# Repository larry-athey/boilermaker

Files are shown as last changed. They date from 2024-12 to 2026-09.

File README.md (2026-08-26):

# Boilermaker

Advanced WiFi enabled ESP32 driven power controller and temperature regulator for brewing and distillation boilers. Multiple units can be combined in a master/slave configuration.

_**NEWSFLASH:** A smaller simplified version called [μBoilermaker (micro Boilermaker)](https://github.com/larry-athey/airhead/blob/main/Instructions/uBoilermaker.md) is now available for sale from my website. These are not WiFi-enabled and use the same guts as the [Airhead](https://github.com/larry-athey/airhead) running in a different operating mode._

You may contact me directly at https://panhandleponics.com<br>
Subscribe to the official YouTube channel at https://www.youtube.com/@PanhandlePonics

**Facebook Idiot:** _Why would you bother?_<br>
**Me:** It's only a "bother" for somebody who couldn't do it on their best day. I'd rather have nicer things.

_...No, I don't use AI to design and build my projects, I actually still know how to use my brain..._

---

<br>

---

After dealing with one cheap Chinese SCR power controller after another I decided to combine one person's email suggestion about building a WiFi enabled PID controller and mash it up with what I had just finished building for Air Still users. PID controllers have their place, but I think they're better suited for 3D printers, fermenters, brew pots, ovens, incubators, etc. The heating element spends more time off than on and that is horribly bad for distilling because there's almost nil upward thermal velocity happening in your boiler.

So I came up with my own controller to overcome all of the shortcomings that I kept running into with others. The Boilermaker has 4 different operating modes.

1. Constant Power (similar to an SCR controller, but leaps and bounds better than an SCR controller)
2. Temperature Cruise (controlled chaos, fast linear temperature rise with a limited risk of scorching)
3. Brewing/Fermentation (PID controller, slow and easy heating with an extreme level of accuracy)
4. Cruise Then Brew (Runs mode 2 until the target temperature is reached and then switches to mode 3)

_**NOTE:** Mode 2 is the same temperature control method used in my [Airhead](https://github.com/larry-athey/airhead) upgrade for Air Stills. The progressive temperature feature is also implemented here and can be used in modes 2 and 3. The only difference here is that the Boilermaker doesn't turn off at the end of the progression unless the countdown timer is enabled._

This controller was designed to run a [zero-crossing trigger solid state relay](https://www.amazon.com/dp/B08FR13GYR) utilizing my custom low speed PWM _(most effective method for heating elements)_. My custom low speed PWM works like an SCR controller slowed down to less than 1/1000 the speed and runs heating elements much more effectively. This controller can also be used with an existing PWM controlled SCR board or a voltage controlled SCR board with a [PWM to voltage convertor module](https://www.amazon.com/dp/B0BG2G5FMX) in the middle.

Heating elements have a slow reaction time, they take time to warm up. An SCR controller divides your AC power sine wave into anywhere from 1000 to 20000 slices and then determines which back-to-back slices are on and which ones are off. Granted, this "works" for heating elements, but it's wasteful and never lets the heating element run at its full potential unless it's at 100%. Anything less just results in a lot of energy wasted by warming up the SCRs instead of the heating element. Exactly what benefit are hot SCRs providing?

In the low speed (0.1 Hz to 1 Hz) PWM that I came up with for the [Airhead](https://github.com/larry-athey/airhead) controller and implemented here, even at 50% power using 0.5 Hz, the heating element runs for 1.25 seconds and rests for 1.25 seconds. Most heating elements run for the full duration of their reaction time. Whereas when using an SCR controller, all heating elements only run for 0.008 seconds 60 times per second. See why a low speed PWM running an SSR is better?

The greatest benefit of this PWM and SSR combination is that it doesn't contribute to premature heating element failure as with the high-speed on/off switching in SCR controllers. SCR phase-angle control generates harmonics _(distortions in the AC sine wave)_ which leads to uneven current distribution, physical vibration, and stress within a heating element. The Boilermaker is actually better for your boiler's longevity!

The Boillermaker uses either a DS18B20 temperature sensor or a thermocouple and a MAX-6675/MAX-31855 amplifier module. If your intention is to only use this controller with a distillation boiler or a meat smoker, then the DS18B20 is perfectly fine since it has an upper temperature limit of 125C/257F. If you need a higher temperature range, you will need to use the [Web API call](https://github.com/larry-athey/boilermaker/blob/main/Instructions/WebAPI.md) with your web browser to select the MAX-6675/MAX-31855 amplifier combo instead.

The Boilermaker also features a complete [Web API](https://github.com/larry-athey/boilermaker/blob/main/Instructions/WebAPI.md) for configuration and control, this is how one master unit controls up to 4 slaves. Each of those slaves can also have up to 4 slaves _(look at it like an Amway pyramid scheme)_. This means that these controllers can be added to all kinds of systems out there that allow the use of external commands or API integration of third party devices and services.

The [RPi Smart Still](https://github.com/larry-athey/rpi-smart-still) system fully supports the Boilermaker in all three temperature managed modes. It can also run the Boilermaker the same way as an SCR controller or gas valve, but without the need for a stepper motor.

_**NOTE:** The Boilermaker is also handy for turning any cheap electric smoker into one that's a whole lot more reliable and accurate, see the [Usage Tips](https://github.com/larry-athey/boilermaker/blob/main/Instructions/Usage-Tips.md) for more information._

<br>
<br>


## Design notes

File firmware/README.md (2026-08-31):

# Firmware Updating

As of the Boilermaker v1.0.3 source code, end users can now update their firmware over-the-air using a web browser. The initial plan was to provide a USB firmware update utility, but the one that Espressif provides doesn't work like the Arduino IDE does and requires the user to perform circus tricks and learn to use a cryptic program that no non-techie will ever bother with.

To put the Boilermaker into firmware update mode, open the following URL with your web browser.

**http://boilermaker-ip/update-firmware** (where "boilermaker-ip" is the IP address of your Boilermaker)

The Boilermaker will start up a WiFi access point with the SSID **"Boilermaker-Updater"** and the password to connect is **"12345678"**.

Now open this URL: **http://192.168.4.1**

<br>

If you are unable to connect, check to make sure that your device pulled an IP address from the Boilermaker. If it does not pull one, you will need to manually configure a static IP address on your device. Here are settings that will work for you if you encounter this problem.

Address: 192.168.4.100<br>
Subnet Mask: 255.255.255.0<br>
Gateway: 192.168.4.1<br>
DNS: 192.168.4.1<br>

Click on the button to browse to your **boilermaker-firmware.bin** file and click the blue button to start the upload.

Once the upload progress bar has completed, the Boilermaker will reboot and will be running the new firmware.

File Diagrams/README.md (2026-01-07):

<br>

The instructions on this page are for my original prototype, shown in the above. It ain't pretty, but I still have my first one running my electric smoker to this day. The units that I sell on my website are based on the [Firefly PCB](https://github.com/larry-athey/boilermaker/tree/main/Diagrams/Firefly-PCB). The prototype model only requires the [Boilermaker-PSU-and-Interface](https://github.com/larry-athey/boilermaker/blob/main/Diagrams/Schematic_Boilermaker-PSU-and-Interface.pdf) to be wired up on a prototype PCB and connected to an ESP32 with breadboard jumper wires.

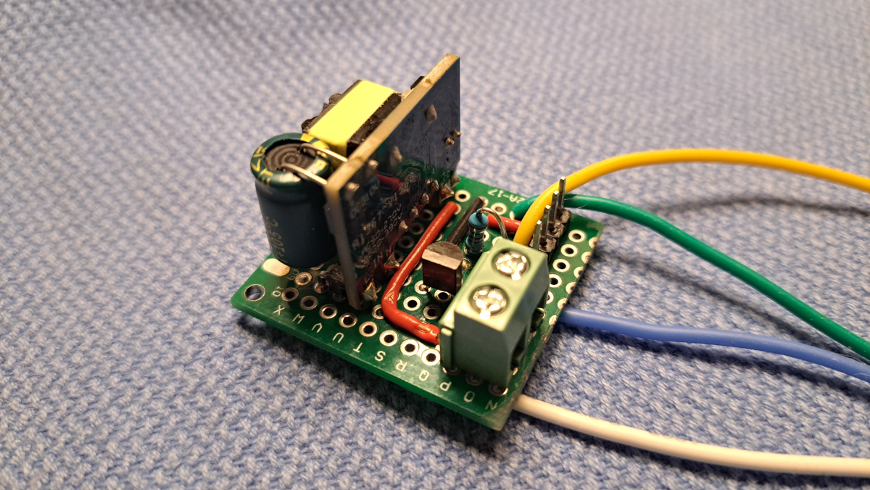
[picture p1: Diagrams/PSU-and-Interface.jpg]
<br>

As you can see, there's a whole lot of nothing to it. 4 wires come from it for the SSR + _(yellow)_, SSR - _(green)_, and two for the AC power input to the power supply _(blue and white)_. The cooling fan connects to the screw terminals _(+ on the left, - on the right)_. The 4-pin header is for the ESP32 for _(left to right)_ the fan trigger, SSR trigger, +5 volts, and ground. This only takes about an hour to assemble.

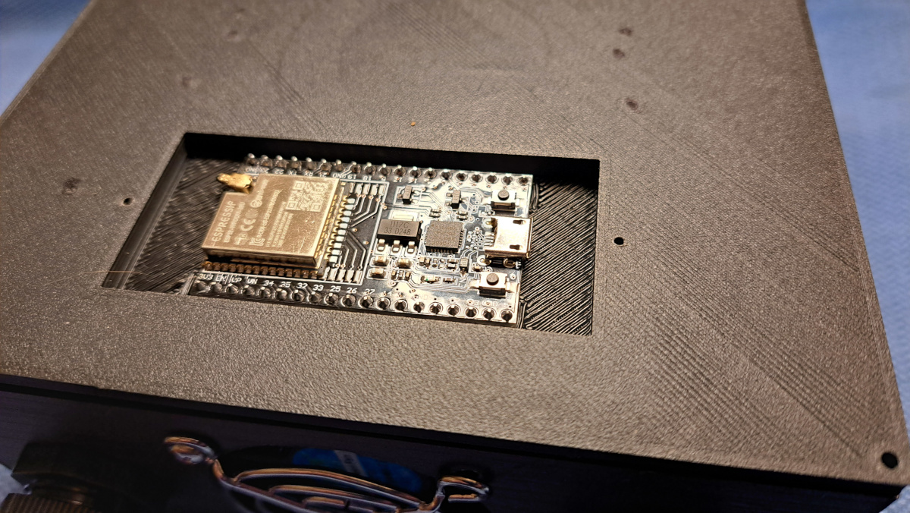
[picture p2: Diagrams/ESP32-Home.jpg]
<br>

As you can see in the **ESP32-Home.jpg** photo in the above, the ESP32 simply rests in the recessed cavity in the case cover. Another cover goes over this _(the **BM-ESP32-Cover.stl** model)_ to keep the ESP32 in place. This cavity is also big enough to hold the LilyGo ABS shell for their standard non-touch T-Display-S3 module. I've used a 38 pin WROOM-DA in this photo with an external antenna.

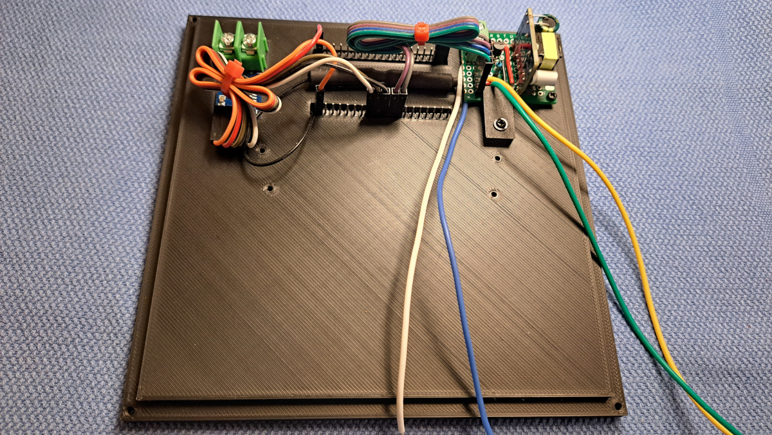
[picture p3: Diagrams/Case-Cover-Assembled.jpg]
<br>

In the **Case-Cover-Assembled.jpg** photo shown above, you can see the placement of the PSU and interface board, the MAX-6675 thermocouple amplifier, and the ribbon cables used to connect everything to the ESP32 pins. The external antenna is located between the rows of the ESP32 pins. If you bundle up the ribbon cables with zip ties, this will keep everything out of the way of the heatsink.

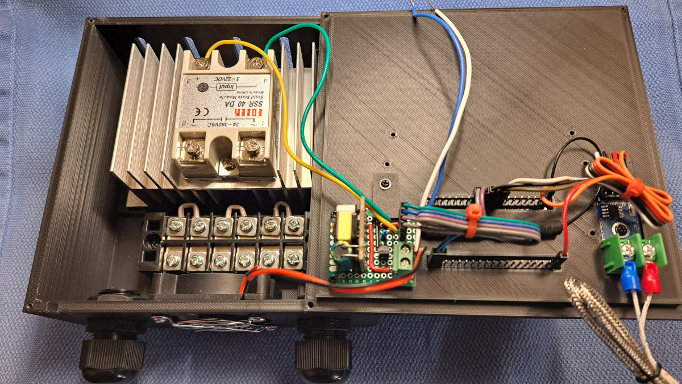
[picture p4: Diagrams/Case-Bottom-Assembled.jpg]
<br>

In the **Case-Bottom-Assembled.jpg** photo shown above, you can see the SSR and heatink as well as a screw terminal bus bar installed in the case bottom. The trigger wires to the SSR are connected and you would connect your AC power input/output lines at this point. Connect the ESP32 PSU input lines to the AC input side of the SSR and the bus bar. Honestly, it's totally up to you if you want to switch the AC hot or neutral line with the SSR, it honestly makes no difference. Connect the fan & thermocouple and you're done.

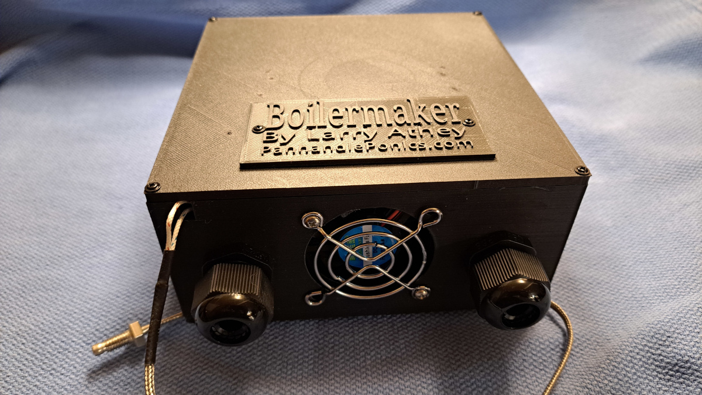
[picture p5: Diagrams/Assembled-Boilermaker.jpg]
<br>

And, as you can see in the **Assembled-Boilermaker.jpg** photo above, you have an assembled Boilermaker that's ready to go. Your choice of SSR will vary, depending on the load that you intend to run. Refer to the last section in the [Usage Tips](https://github.com/larry-athey/boilermaker/blob/main/Instructions/Usage-Tips.md) document for more information. While the amperage rating is important, the size of the heatink and having a cooling fan are equally important. You can very easily blow an SSR-100DA with a mere 1500 watt load if you don't keep it cool enough.

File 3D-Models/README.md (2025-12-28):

<br>

This case should print just fine on any 3D printer since it's not unnecessarily large. However this will not be a quick print due to the thickness of the walls, which is necessary since PLA printed items will warp if exposed to escessive heat. I'm not even joking for a minute, on a Creality Ender 5 Pro running at standard resolution and using 30% infill, the top of the case takes 8.5 hours and the bottom takes 21 hours with no supports. Making the walls thinner and reducing the infill doesn't have that much effect on the time.

_**NOTE:** You are free to use any resolution and infill rate of your choosing. I just use 30% infill by default for everything in order to make top surfaces smoother. The difference in print time between 15% and 30% isn't enough to make me lower my standards._

Using my settings with no supports for the bottom or ESP32 cover and the required supports for the ESP32 opening in the lid, below are the weights of each item so you will know how much filament that you need to have left on your roll.

Bottom - 185 grams<br>
Lid - 95 grams<br>
ESP32 Cover - 10 grams<br>

I intend to sell Boilermakers as assembled and tested units _(and pre-configured for the customer's WiF network)_, and I really can't afford to send out units where the case will warp due to excessive internal heat. $30 for a weather-proof ABS outdoor utility enclosure also doesn't make sense to me for something like this. Especially since a 1 KG roll of PLA filament is only $23 and I could print 5 cases.

This case was designed to accommodate an [SSR-40DA](https://www.amazon.com/Inkbird-Solid-Thermostat-Temperature-Controller/dp/B00HV974KC/) mounted to a [large SSR heat sink](https://www.amazon.com/uxcell-Aluminum-Dissipation-Single-10A-100A/dp/B07C8R7MS2/), and supports both a standard or wide format [38 Pin ESP32](https://www.amazon.com/gp/product/B09J95SMG7/). The ESP32 mounts in the lid and requires an additional cover _(**BM-ESP32-Cover.stl**)_ to be 3D printed to keep it in place.

The top of the case has a recessed footprint to mount a MAX-6675 thermocouple amplifier and screw holes to mount an Airhead PSU and Interface PCB. You will want to raise it with 1/4" spacers to allow room for jumper wire connections to the ESP32. It also provides screw holes for mounting various sizes of [prototye boards](https://www.amazon.com/ELEGOO-Prototype-Soldering-Compatible-Arduino/dp/B072Z7Y19F/) if you intend to build the PSU and interface according to the schematic in the **/Diagrams/** directory here. Use the **BM-PCB-Clamp.stl** to clamp down the side opposite of the screw holes.

This case also provides a footprint to mount a 6-column 90mm bus bar in the bottom for all AC power connections, and includes holes for 1/2" strain reliefs in case you decide to sacrifice a 12 gauge extension cord. Holes in the bottom of the case to the left and right of the bus bar are also provided in the event that you want to wall mount the unit.

There is also a 50mm fan mounting footprint between the AC power cable holes. You should install your fan so that it pulls cool air through the heat sink and evacuates the heat from the case. With most fans, this would mean the label side faces outward. I'd also suggest using a fan that comes with a guard/grill. This fan only runs when the Boilermaker is active so as not to fill it up with dust like a computer's cooling fan does.

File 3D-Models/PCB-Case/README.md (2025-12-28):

# 3D Model Notes

The models in this directory are for use with the PCB designed by [FireflySE](https://github.com/FireflySE) of Sweden. If you intend to sell assembled and tested Boilermakers, you will want to use the PCB and this case to make things easier on yourself. This case is 20mm longer than the one for prototype build and uses a different cover. This case is also 10mm taller in order to better accommodate 100 amp solid state relays.

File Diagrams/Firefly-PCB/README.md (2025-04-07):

# About this PCB

This is designed by [FireflySE](https://github.com/FireflySE) of Sweden, the same guy who designed the RPi Hat for the [RPi Smart Still](https://github.com/larry-athey/rpi-smart-still) controller system.

This board supports both, type-k thermocouple or DS18B20 temperature sensors. There is a [new version](https://github.com/larry-athey/boilermaker/tree/main/3D-Models/PCB-Case) of the Boilermaker case for use with this PCB. The origiinal case doesn't provide enough room to fit the PCB between the fan and SSR heatsink.

_**NOTE:** You will need to make one minor modification to my source code to work correctly with this PCB. My original code has the FAN_OUT constant pointing to GPIO 16, this PCB has it on GPIO 2. I have no idea what the reason was for the switch._

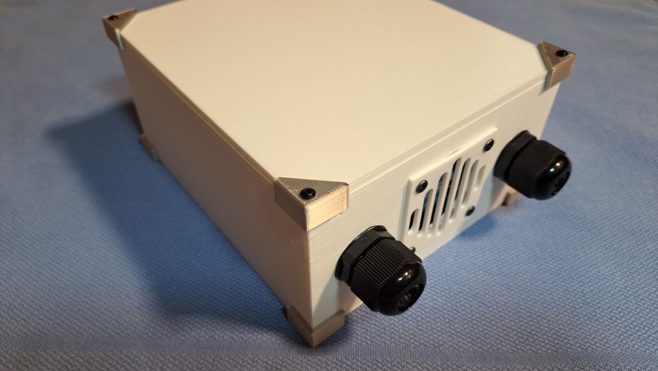
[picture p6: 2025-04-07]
3D-Models/PCB-Case/Boilermaker-1.jpg

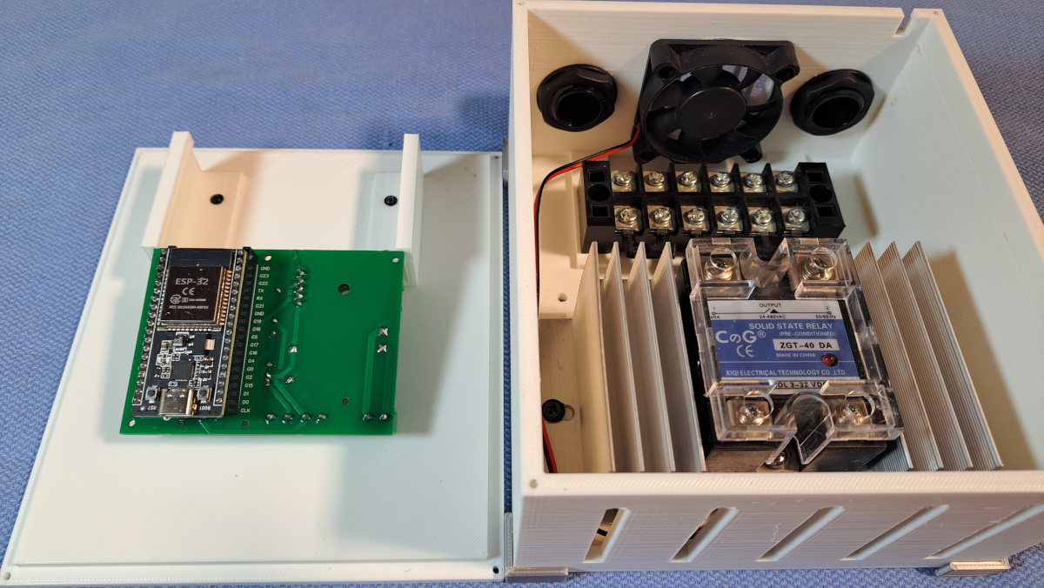
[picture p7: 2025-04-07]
3D-Models/PCB-Case/Boilermaker-3.jpg

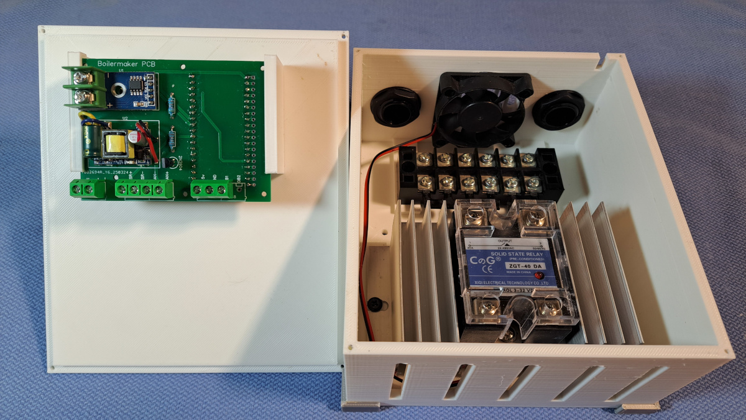
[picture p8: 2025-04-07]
3D-Models/PCB-Case/Boilermaker-2.jpg

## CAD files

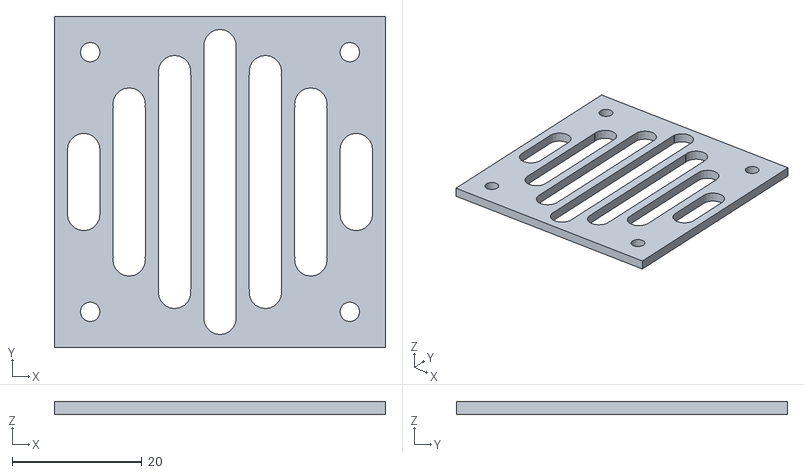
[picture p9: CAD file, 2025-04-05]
3D-Models/BM-Fan-Cover.stl
51.0 x 51.0 x 2.00

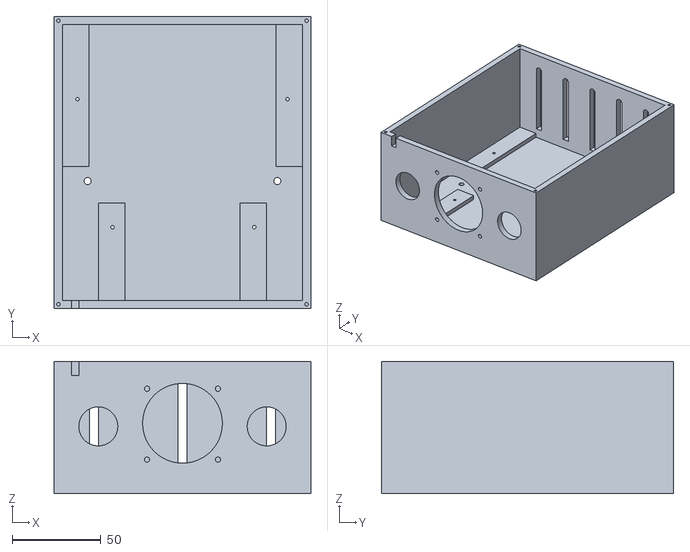
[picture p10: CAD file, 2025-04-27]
3D-Models/PCB-Case/BM-Case-Bottom.stl
145.0 x 165.0 x 74.8

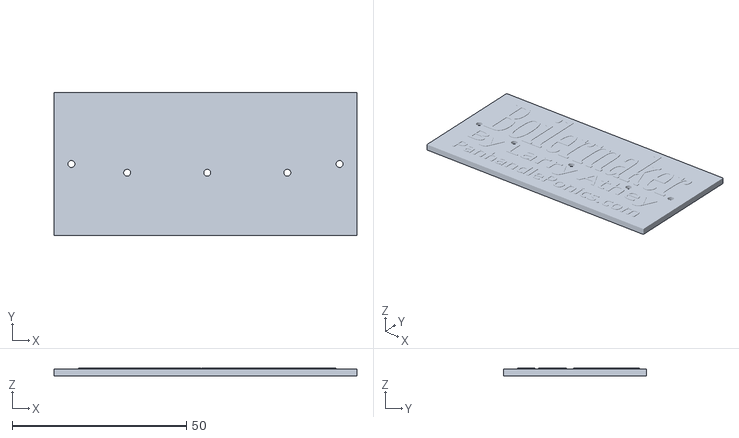
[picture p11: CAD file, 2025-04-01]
3D-Models/BM-ESP32-Cover.stl
87.0 x 41.0 x 2.25

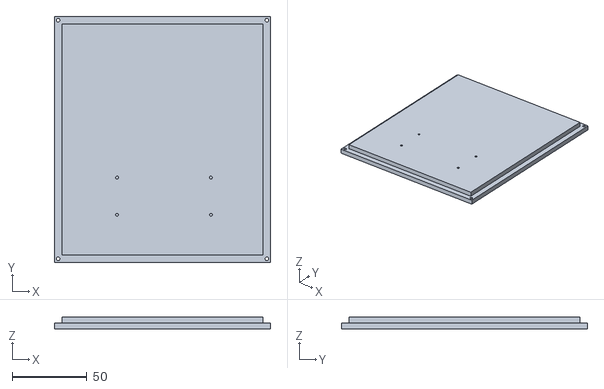
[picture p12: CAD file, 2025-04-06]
3D-Models/PCB-Case/BM-Case-Top.stl
145.0 x 165.0 x 8.00

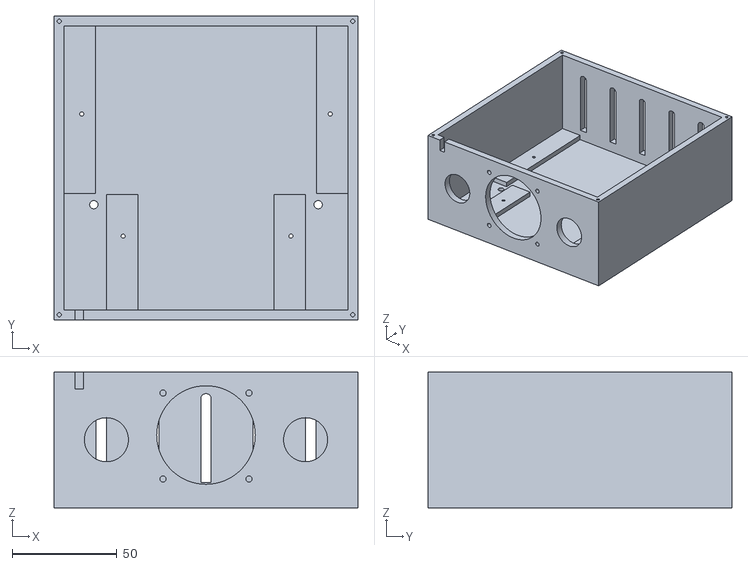
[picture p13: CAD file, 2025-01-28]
3D-Models/BM-Case-Bottom.stl
145.0 x 145.0 x 64.8

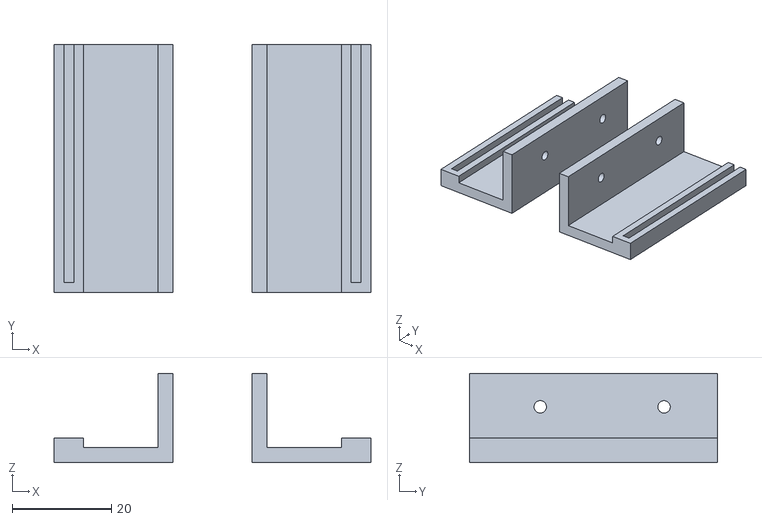
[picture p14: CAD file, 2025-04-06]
3D-Models/PCB-Case/BM-PCB-Mount.stl
64.0 x 50.0 x 18.0

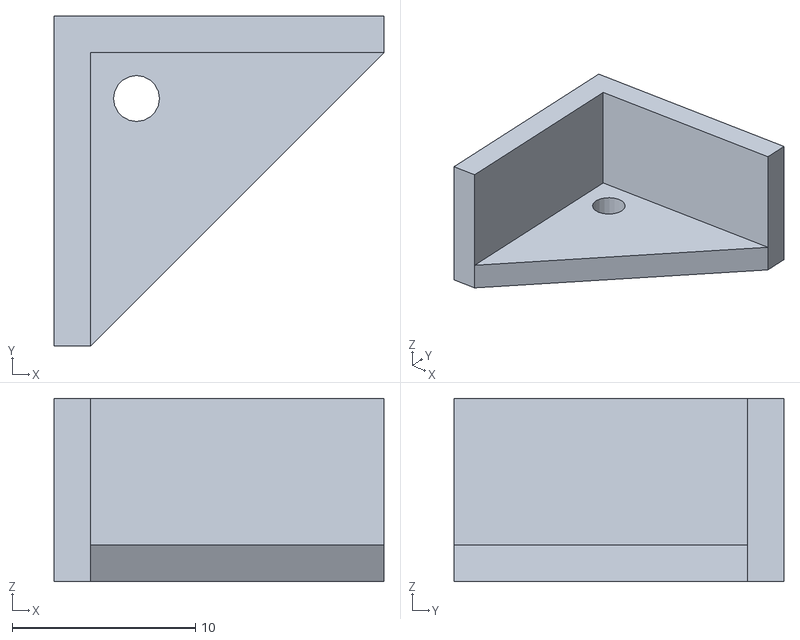
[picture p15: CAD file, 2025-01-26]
3D-Models/BM-Corner-Cap.stl
18.0 x 18.0 x 10.0

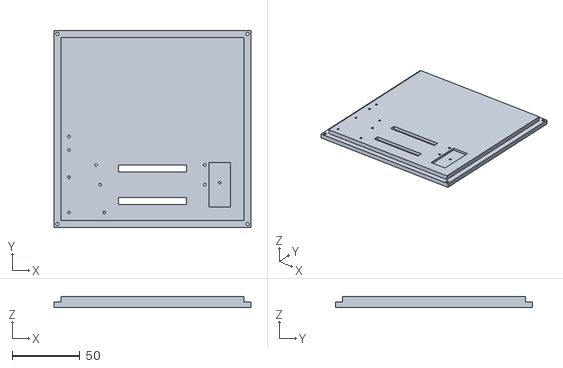
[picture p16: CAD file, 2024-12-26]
3D-Models/BM-Case-Top.stl
145.0 x 145.0 x 8.00

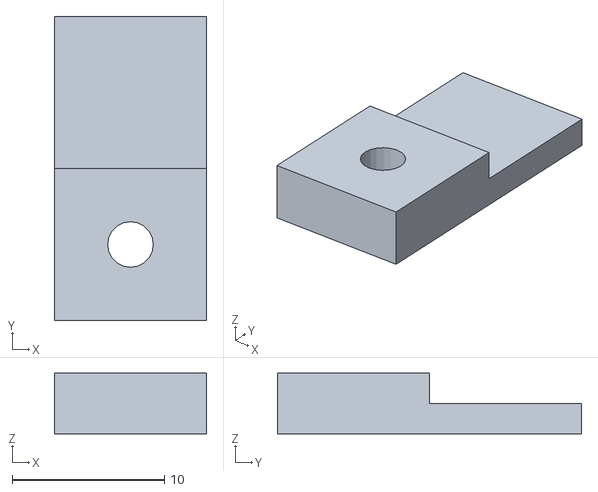
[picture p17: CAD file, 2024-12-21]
3D-Models/BM-PCB-Clamp.stl
10.0 x 20.0 x 4.00

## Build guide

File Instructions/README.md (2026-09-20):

# Instructions

<br>

_**IMPORTANT:** Please keep in mind that where you put your temperature sensor matters! No matter what you are using your Boilermaker for, you absolutely DO NOT want to be reading the temperature of your heating element! You need to be monitoring what you are boiling or the air around what you are smoking/roasting._

_**SECONDLY:** If your system appears to stop reading temperature changes when your temperature sensor comes in contact with your boiler, this means that your hot and neutral lines to the Boilermaker's internal power supply or the AC outlet itself are revesed. A quick (however unsafe) solution is to lift the ground connection, but you really should correct the polarity of the hot and neutral wires._

Unlike other WiFi enabled ESP32 powered devices, the Boilermaker does not default as a WiFi access point in order to configure it. I'm already using nearly 75% of the available code space, I don't want to waste the remaining 25% on a one-time-use feature. I'm reserving that 25% for future features and enhancements, so the WiFi configuration and a few other things are configured over a USB cable and a plain old terminal program. Windows doesn't include one by default anymore, but [PuTTY](https://www.putty.org/) is still free and open source.

[Here's how to use PuTTY under Windows to connect to the Boilermaker.](https://x.com/i/grok/share/i61lGPHt1tv3cxOr8ogD5S6SR)

Mac OS users should install the free [CoolTerm](https://freeware.the-meiers.org/) program, which is also available for Linux desktop systems, including Raspberry Pi systems. Linux users can also install any of the many command line terminal programs with their package manager, such as minicom or picocom. Mac OS also contains a command line terminal simply called "screen". Seriously, serial terminal programs are as old as mainframe servers, this is far from anything new.

_**NOTE:** You can also connect to the Boilermaker with your mobile phone [according to Grok](https://x.com/i/grok/share/BJil4zNbj3p3dYd8i8HHYdEaw) but I haven't tried this yet. You can also simply use the serial terminal in the Arduino IDE by pressing CTRL+Shift+M._

Windows users will also need to download and install the [CP210x driver](https://www.silabs.com/developer-tools/usb-to-uart-bridge-vcp-drivers?tab=downloads) so the Boilermaker will appear as a serial port that your terminal program can connect to. Linux and Mac OS users need not bother with this since the driver is already part of the kernel tree. This driver is actually used with numerous devices, not just ESP32 micro controllers.

Once your Boilermaker is connected to your computer with a USB data cable _(not just a charging cable)_, it will appear as a serial port and your terminal program will see it. The communications parameters are 9600 baud, 8N1. This is an old standard and shouldn't require any special configuration steps on your part.

Once you are connected, press your Enter key to refresh the screen and you will see the following in your terminal. As you can see, the serial terminal is only used for configuring network related settings and a temperature sensor offset in the extremely rare event that you have an inaccurate sensor. No need for the added bloat of an access point and web configutator.<br>

Serial Configuration Menu

_**IMPORTANT:** Since this project relies on ESP32 v2.14 to v2.17 board libraries, it only supports WPA2 WiFi networks. While it might connect to a WPA3 network at startup, it will repeatedly fall offline and attempt to reconnect every minute. Especially if your router uses a single SSID and band steering (turn that off, use separate SSIDs for each band). If your router cannot be switched to WPA2 mode, you will need a separate WiFi access point (not an additional router or WiFi extender) for the Boilermaker. TP-Link's budget EAP or WA series are great options._

The menu options are as follows:

**0. Set Device Name** - This is where you give your Boilermaker a personalized name. This will be displayed in the Web UI and is also used as its hostname when it announces its presence on your network.

**1. Set SSID** - This is where you set the WiFi network name that you want to connect to.

**2. Set Password** - This is where you set the WiFi network password.

**3. Set DHCP or Static IP** - This is where you tell your Boilermaker to ask your router for an IP address, or you specifically set an IP address that never changes. It's far beyond the scope of this document to explain how IP addresses and TCP/IP standards work. I will just say that you will make life a lot easier for yourself if you set a static IP address. Otherwise, you will need to go into your router configuration and create a reservation for your Boilermaker so that it gets the same IP address every time.

**4. Connect to WiFi** - Use this option to test your WiFi configuration. Once you can see that your Boilermaker connects to your WiFi, you won't have to worry about it again unless you change your WiFi netwoork name or password. Your Boilermaker will automatically connect to your WiFi network at startup, and will check its connection once per minute and automatically reconnect if necessary.

**5. Set Slave 1 IP** through **8. Set Slave 4 IP** - This applies to all four slave IP address settings. Any Boilermaker can control up to 4 more Boilermakers, whether they are being used as a master or a slave. Which means that every slave can also have up to 4 slaves. You simply provide the IP address of other Boilermakers and they will automatically follow this one's power level and run status.

**9. Set Correction Factor** - In the extremely rare event that you got a temperature sensor that isn't reading correctly, you can enter a number from -5.00 to +5.00 (C) here to shift its readings up or down. Even at that rate, 5 degrees (C) in either direction would tell me to just replace the sensor. But, the option is here in case you ever need it.

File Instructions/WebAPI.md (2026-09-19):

# Web API Usage

The WebUI communicates with the Boilermaker using HTTP API calls since it's a single page web user interface that dynamically updates using Ajax refresh. All settings except for the WiFi configuration can be configured using plain old HTTP GET requests, which means you can configure pretty much everything just by typing URLs into your web browser's address bar. WiFi configuration has to be done via serial connection because you can't use the WebAPI unless it's already connected to WiFi.

If you use **curl** in Linux or Mac OS to configure it, you have to tell it to use an old HTTP protocol. This is because there is limited code space in an ESP32 and modern HTTP protocols would have an absolutely huge code footprint. For example, if your Boilermaker has the IP address 192.168.1.150 and you wanted to read the current temperature in Celcius, you would use this command.

`curl -s --http0.9 http://192.168.1.150/get-tempc`

The `-s` option silences the network traffic progress that **curl** normally prints on the screen so all you get is the temperature value, and the `--http0.9` tells **curl** what HTTP protocol to use. If you don't specify the 0.9 protocol, you will only get an empty result.

_**NOTE:** This API only returns JSON objects for success or failure when setting values. Requested values are returned as-is, plain text. The ESP32 has limited code space and storing text strings eats up more space than plain old evaluation code. If I was dealing with unlimited code space like you have on any actual server running PHP, I'd be telling a different story here._

## Boilermaker API Call Listing

Not passing any API call or making an invalid API call will return the entire home page of the WebUI.

**/ajax-livedata** - Used by the WebUI to update the second data card on the screen.

**/ajax-settings** - Used by the WebUI to update the third data card on the screen.

**/ajax-timer** - Used by the WebUI to update the fourth data card on the screen.

**/ajax-progress** - Used by the WebUI to update the fifth data card on the screen.

**/?data_0=** - Primarily used by the WebUI to set the Operation Mode of the Boilermaker. Passing a value of 0 sets it to Constant Power, 1 sets it to Temperature Cruise, 2 sets it to Brewing/Fermentation, 3 sets it to Cruise Then Brew, 4 sets it to PID Auto Tune. If you have slaves configured, all slaves will be switched to Constant Power mode when a run starts and will follow all power adjustments made by the master. Changes to this will not be honored if there is an active run.

**/?data_1=** - Primarily used by the WebUI to set the Target Temperature of the Boilermaker. The value passed here is the temperature in Celcius and must be a whole or floating point number between 0 and 260. If you are using this Boilermaker with the **RPi Smart Still** controller system, this value will be set lower boiler range temperature of your program when you start a run, and will be dynamically adjusted upward if you have the Progressive Temperature feature enabled.

**/?data_2=** - Primarily used by the WebUI to set the Startup Power of the Boilermaker. The value passed here must be a whole number between 10 and 100. Adjusting this value during an active Constant Power run will update the current power level.

**/?data_3=** - Primarily used by the WebUI to set the Fallback Power of the Boilermaker. The value passed here must be a whole number between 10 and 100. Adjusting this value during an active Constant Temp run will only work if the Boilermaker hasn't yet reached the target temperature.

**/?data_4=** - Primarily used by the WebUI to set the Adjustment Rate of the Boilermaker. The value passed here must be a whole number between 1 and 100. Adjusting this value during an active Constant Temp run will work at any point during the run.

**/?data_5=** - Primarily used by the WebUI to set the Deviation Rate of the Boilermaker. The value passed here is the temperature in Celcius and must be a whole or floating point number between 0.1 and 5. Adjusting this value during an active Constant Temp run will work at any point during the run.

**/?data_6=** - Primarily used by the WebUI to set the Change Wait of the Boilermaker. The value passed here must be a whole number between 1 and 1000 (seconds). Adjusting this value during an active Constant Temp run will work at any point during the run.

**/?data_7=** - Primarily used by the WebUI to set the Rest Period of the Boilermaker. The value passed here must be a whole number between 1 and 1000 (seconds). Adjusting this value during an active Constant Temp run will only work if the Boilermaker hasn't yet reached the target temperature.

**/?data_8=** - Primarily used by the web UI to set the PID proportional gain value. The value passed here is a floating point number between 0.1 and 15.0 and will not be honored if there is an active run.

**/?data_9=** - Primarily used by the web UI to set the PID integral gain value. The value passed here is a floating point number between 0.001 and 0.5 and will not be honored if there is an active run.

**/?data_10=** - Primarily used by the web UI to set the PID derivative gain value. The value passed here is a floating point number between 0.0 and 2.0 and will not be honored if there is an active run.

**/?data_11=** - Primarily used by the web UI to set the PID sample time value. The value passed here is a floating point number between 5.0 and 30.0 and will not be honored if there is an active run.

**/?data_12=** - Set the SSR low speed PWM duty time. The value here is a whole or floating point number between 1 and 5 _(seconds)_. The magic number for your system depends on the wattage and intended supply voltage of your heating element(s). If you are using a 1000 watt 240 volt element running on 120 volts, you would likely be better off with a 2.5 second duty time due to the slower reaction time of the element. If it's a 1000 watt 120 volt element at 120 volts, then you'll probably want a 1 second duty width. The slower the reaction time, the wider the duty time should be. If using this code with an SCR board, this is not a valid API call. You will need to restart your run to make this setting take effect.

**/?data_13=** - Primarily used by the web UI to set the progressive temperature feature on or off. The value passed here must be a whole number between 0 and 1 and will be rejected if there is an active run.

**/?data_14=** - Primarily used by the web UI to set the progressive temperature range. The value passed here must be a whole number between 1 and 50 for degrees celcius to add to the target temperature and will be rejected if there is an active run.

**/?data_15=** - Primarily used by the web UI to set the progressive temperature time. The value passed here must be a whole number between 1 and 24 hours and will be rejected if there is an active run.

**/?data_16=** - Primarily used by the web UI to set the countdown timer feature on or off. The value passed here must be a whole number between 0 and 1 and will be rejected if there is an active run.

**/?data_17=** - Primarily used by the web UI to set the countdown timer run time. The value passed here must be a whole number between 1 and 1440 minutes and will be rejected if there is an active run.

**/form-0** through **/form-17** - Used by the WebUI to dynamically generate the various settings editor forms for the **/?data_*=** hooks.

**/get-correctionfactor** - Returns the current temperature sensor correction factor in Celcius.

**/get-power** - Returns the current power percentage level.

**/get-runtime** - Returns the total elapsed seconds of the currently active run, or zero if there is no active run.

**/get-slaveip1** through **/get-slaveip4** - Returns the IP address of the requested slave unit and will return 0.0.0.0 if the requested slave unit is not configured.

**/get-ssrpwm** - If using this code with an SSR and low speed PWM, this returns the duty width of the PWM in seconds. If using this code with an SCR controller, this is not a valid API call.

**/get-sensortype** - Returns the selected temperature sensor type. 0=MAX-6675/MAX-31855, 1=DS18B20

**/get-tempc** - Returns the current measured temperature in Celcius (after correction factor).

**/get-tempf** - Returns the current measured temperature in Fahrenheit (after correction factor).

**/get-uptime** - Returns the current system uptime in seconds.

**/get-wifistats** - Returns the current WiFi channel and signal level as two formatted lines of text. Keep in mind that a signal level of -40 is stronger than -50, the closer to zero the stronger the signal.

**/?power=** - Performs a power jump during an active Constant Power run without affecting the Startup Power setting stored in memory. The value passed here must be a whole number between 10 and 100. If you are manually controlling slaves, you must first put the slave in Constant Power mode and then start it before making this call or or the slave will start up at its pre-programmed Startup Power level.

**/reboot** - Reboots the Boilermaker. _(Any surprise there?)_ If you use **/get-uptime** and see that the Boilermaker has been running anywhere near 49 days, you should reboot it before starting a run because the internal code could reboot the unit in the middle of your run if you hit its maximum allowed uptime of 49.7 days.

**/?set-correctionfactor=** - Set a new temperature sensor correction factor. The value passed here is a temperature in Celcius and must be a whole or floating point number between -15 and 15. If you are using a sensor mounted outside of the boiler, such as when the sensor is mounted to the bottom like an Air Still. You will need to use a positive correction factor since it will be reading lower than the actual contents of the boiler. For example, the Airhead uses a +5 correction factor in most cases.

**/?set-sensortype=** - Set a new temperature sensor type. 0=MAX-6675/MAX-31855, 1=DS18B20

**/?set-slaveip1=** through **/?set-slaveip4=** - Set the IP address of the 4 possible slave units. This can be either IPV4 or IPV6 format. Setting a slave's IP to **0.0.0.0** will unassign that memory slot.

**/start-run** - Used to start a run.

**/stop-run** - Used to stop an active run.

**/toggle-run** - Primarily used by the WebUI to toggle the active run state of the Boilermaker.

**/update-firmware** - Used to reboot the Boilermaker in firmware update mode, refer to the **/firmware/** directory of this GitHub repository for more information. This only works if there is currently _not_ an active run.

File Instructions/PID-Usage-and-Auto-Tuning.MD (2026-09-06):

# PID Usage and Auto Tuning

_This document is only intended for the Boilermaker, not any other controller with PID support, and is not a complete PID tutorial._

Many people think that a PID controller is the be-all and end-all to temperature and power controllers. This is actually anything but the truth. However, PID controllers have their place and shine in some areas, but pale in others. The only time that a PID controller is of any use in distillation is if you are running at a full boil, but you damn well better have a dephlegmator in your column or you're gonna get a lot of heads and tails, and some really watered down distillate.

If you own an Air Still (or clone) with the Airhead upgrade installed, do a progressive test run in Airhead mode (PI mode). Then re-run the distillate again (dump it back in the still) with the unit running in μBoilermaker mode (PID mode) using the same progressive run settings. You'll be lucky if you get a full shot glass of distillate.

### What is PID? (simple version)

PID is a control method that tries to reach and hold your exact target temperature smoothly:

- **P (Proportional)** — How strongly it reacts to being off-target.
- **I (Integral)** — Corrects small long-term errors (like slowly drifting a bit low).
- **D (Derivative)** — Looks at how fast the temperature is changing and helps prevent overshooting.

### And now the scientific version

<br>

In the Boilermaker's **Temperature Cruise** mode (PI mode), the **Change Wait** and **Adjustment Rate** are equal to the **P** parameter and the **Deviation Rate** is equal to the **I** parameter.

### Realistic Expectations

- PID gives very steady temperature — great for mashing, fermenting, sous-vide style control, or electric smokers.
- It is **not** as thermally aggressive as the Boilermaker's PI mode. Once at temperature it will pulse the heater more gently, so you will see significantly slower vapor production in distillation.
- The temperature control becomes more stable the longer it runs because the PID is training itself on the current load.
- Autotune results are a good starting point, but every boiler/setup is different. Feel free to tweak the numbers ±20–50% and test.

### PID Auto Tuning

The first thing you need to do here is be **absolutely** aware of the fact that auto tuning is only meant to be used as an initial point to begin fine tuning from, this is not a magic bullet that saves you from having to learn how PID controllers work.

This procedure is not a fast process and requires your boiler to be completely filled to its full line. This procedure also preheats the boiler to 66C/150F before the tuning begins, so don't run this if you're in a hurry. Lastly, once you start it, you only have 15 seconds to stop it because the web UI will become completely unresponsive until the procedure completes.

You may want to preheat your boiler yourself so you aren't sitting there for an hour or more wondering how far along things are. It also doesn't hurt to preheat the boiler to the temperature that you actually intend to run at. All that matters is that there's ample space between that temperature and the boiling point of water at your altitude.

Once the PID auto tuning procedure completes, you will see the **Tuning Data** line display a string of text like this.

**Ku=0.102 Dt=160.2 Tau=163.0 → Kp=0.647 Ki=0.003 Kd=0.012 (valid=1)**

- Ku — process gain (how strongly temperature responds to a change in heater power).
- Dt — dead time in seconds (lag between applying power and the first noticeable temperature change).
- Tau — time constant in seconds (how long the temperature takes to cover most of its eventual change after the dead time).
- Kp / Ki / Kd — the proportional, integral, and derivative gains calculated from Ku, Dt, and Tau using the selected tuning rule.

The main element that you need to be concerned with is the last one, **valid=1** means that it completed without error. If you see **valid=0** then the tuning failed and your P/I/D settings will not be updated. If any of the first three elements are zero or if the Kp/Ki/Kd elements are outside of the valid ranges allowed by the web UI, it will be flagged as a failure.

If you have an inefficient boiler setup, then you will likely see a lot of failures. This would include under-sized heating elements for the amount of water volume, or a boiler that loses heat too easily. If the Boilermaker is sending power to your heating element and the temperature sensor sees too little change in a given time frame, this will cause the PID auto tuning to fail.

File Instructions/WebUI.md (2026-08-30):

# Web User Interface

<br>

_**NOTE:** The Boilermaker uses a fully text mode user interface rather than a fancy graphics based interface because it doesn't rely on a centralized server like regular mobile apps do. Sorry, no fancy dial/slider controls and sound effects here, I'm not a mobile app developer._

The WebUI is designed for cell phone screens in vertical/portrait mode. It will still work on desktop/laptop/tablet screens, but will appear stretched out. I would add more code to fine tune it to be more friendly to larger screen sizes, but I'm working with a limited amount of code space in the ESP32 and I already have it 75% full. If you must use it on a desktop PC, use Firefox and switch it into mobile app view by pressing **CTRL+Shift+M** _(or **Command+Option+M** if you are using a Mac)_.

The Boilermaker code is derived from the [Airhead](https://github.com/larry-athey/airhead), which is a port of PHP to C++ from my [RPi Smart Still](https://github.com/larry-athey/rpi-smart-still) boiler management routines. What I've done with the Boilermaker is make various static variables in the Airhead code, user configurable options in the WebUI. The Air Still is a 700 watt heating element coupled with a 1 gallon boiler vessel. The default settings here are the Airhead parameters scaled up to work with a 7 gallon Still Spirits boiler. This should help you adjust the settings to match your boiler.

## First WebUI Data Card

In the first card at the top of the WebUI, you see the device name and the number of configured slave units. Remember, the device name is also its network host name. If you are using DHCP configuration for your WiFi and your router assigns your Boilermaker a new IP address, you will want to look for this name in your router's admin page where it shows the connected 2.4 GHz devices. To avoid this problem, you should assign your Boilermaker a static IP address outside of the router's DHCP pool, or have your router create an IP reservation for your Boilermaker.

The second line here that shows how many configured slave units you have, also shows how many of them are online and responding to pings. You should make sure that your slave units are online before you start a run. Otherwise, you will need to manually switch them constant power mode and then start them after your master unit has started. The HTTP API commands from the master to put slaves in the correct operating mode and start them is only sent once and only if they are pinging.

_**NOTE:** The start/stop button has an immediate effect on the Boilermaker, but you may not see the run status change on your screen for 4 or 5 seconds. There is not a constant data stream between your web browser and the Boilermaker, it uses random timed Ajax refresh calls. If you have slave units configured, this update will take even longer because your Boilermaker needs to make API calls to all of the slaves to start and stop them and set their power level. Don't get impatient and repeatedly press the start/stop button!_

## Second WebUI Data Card

The second WebUI card displays live data from the Boilermaker. This data in the following two WebUI cards is updated at a random time period anywhere from 4.5 to 5.5 seconds. There is not an actual continuous data stream between your cell phone and the Boilermaker, your phone only requests data updates from it at random times.

**Run State:** This will say "Inactive" in yellow letters if the Boilermaker is idle, or it will say "Active" in red flashing letters if it is actively running your heating element. If progrssive temperature is enabled, it will say "Progressive" while in progress and then say "* Active" once the progression is complete.

**Uptime:** This shows how long your Boilermaker has been running without a restart in Hours:Minutes:Seconds. Keep in mind that ESP32 units only have a timer, not a real time clock. These will only run for 49.7 days before the timer rolls over to zero. The Boilermaker code will reboot the device at that point and that would be a bad thing to happen in the middle of a distillation run.

**Runtime:** This shows how long the current run has been active.

**Countdown:** Only visible when the timer is active. Shows the amount of runtime remaining.

**Temperature:** Shows the current temperature whether or not there is an active run.

**Power Level:** Shows the current power level during an active run.

## Third WebUI Data Card (first two operation modes)

The third WebUI card displays all of the user configurable settings. These values are also updated on a random time basis since the Boilermaker has a complete HTTP API which allows it to be remotely configured by another device on the network. Tapping/clicking on any of the values shown in light blue will make a popup form appear so you can edit these as you choose. Keep in mind that the ESP32 is only a 240 MHz computer, its web server is a bit laggy. Sometimes it takes a couple seconds for the form to display.

**Current Mode:** This will say "Constant Power", "Temperature Cruise", "Brewing/Fermentation", "Cruise Then Brew", or "PID Auto Tune".
1. **Constant Power** will run the unit like any other SCR power controller, but runs your heating element(s) more effectively.
2. **Temperature Cruise** will honor a target temperature and manage the power in order to maintain that temperature using high thermal velocity. This is the same temperature management method used in the [Airhead](https://github.com/larry-athey/airhead) upgrade for Air Stills. The technical definition of this mode would be a PI controller, but with more configurability.
3. **Brewing/Fermentation** is a strict, yet adjustable, PID controller that is geared by default for slow and steady temperature management, not distillation due to its reduced thermal velocity.
4. **Cruise Then Brew** is meant to quickly preheat your mash/wort in **Temperature Cruise** mode and then automatically switch to **Brewing/Fermentation** mode after it reaches the target temperature. Refer to the [Usage Tips](https://github.com/larry-athey/boilermaker/blob/main/Instructions/Usage-Tips.md) guide for more information on the reasoning for this feature.
5. **PID Auto Tune** should be used with care because this will make your Boilermaker completely unresponsive until the tuning procedure is complete, the only output is via the serial connection. You only have 15 seconds to cancel it if you accidentally start it. Otherwise, you will need to disconnect the power and plug it back in. There are no adjustment parameters for this mode. The time this takes is completely up to your boiler's physical attributes. Your boiler needs to be full of water, it will be raised to 66C/150F before the tuning begins which takes 10 to 20 minutes. If you don't want to be stuck in the dark wondering what's going on for a long time, preheat your boiler to 63C/145F before starting the PID auto tuning procedure.

**Target Temp:** As the name implies, this is the target temperature that you want to shoot for. Everything is done in Celcius at the hardware level, so you need to enter your choice in Celcius here. The upper limit is 260C/500F, and will require you to use a thermocouple instead of a DS18B20 for anything over 125C/257F. This will allow you to use a Boilermaker to run an electric oven or any other high temperature electric appliance.

**Startup Power:** This parameter has two purposes. In Constant Power mode, this is the power level that the Boilermaker runs at. In Temperature Cruise mode, this is where your power level starts at as it slowly increases the power level until the **Target Temp** has been reached. 50% is a good starting point and also helps reduce the possibility of scorching suspended solids. If you change this value during an active Constant Power run, the current power level will be updated to the new value.

**Fallback Power:** As mentioned in the above, in Temperature Cruise mode, the Boilermaker starts out at one temperature and slowly increases power until the **Target Temp** has been reached. If you were to simply stop right there, you would quickly overshoot the target, especially if you're at 100%. So, after the **Target Temp** is reached, the Boilermaker has to fall back to a point and then begin temperature management by working up to the required power level. 50% is a good starting point, you will just have to tinker with settings to find the magic number for your setup.

**Adjustment Rate:** This parameter is how much your power is progressively adjusted over time to reach the **Target Temp**. This is also how much to adjust the power up or down when a temperature correction is needed. The temperature management here works exactly like the cruise control in a car. It progressively gets more and more gas to get up to speed, and then falls back. Then the gas is increased or decreased by a certain amount with a delay between adjustments to stay locked on the target speed.

**Deviation Rate:** This parameter determines how much temperature drift is allowed before a correction is required. The default values that I've provided here should be a good starting point for most people, but you will need to tinker with settings to find the magic number for your boiler. You don't want to keep this number too low or you will bog down the ESP32. You also don't want to go too high or you will have yo-yo temperatures. Remember, large volumes of water do not change temperature quickly.

**Change Wait:** As your Boilermaker starts up, this is the amount of time between each **Adjustment Rate** change as it works its way up to **Target Temp**. This is also the amount of time between temperature correction power adjustments. This provides time for the last power adjustment to affect the temperature of the boiler before deciding what the next adjustment should be.

**Rest Period:** After your boiler has reached **Target Temp**, the power decreases to **Fallback Power**, then the Boilermaker rests for a period of time to allow any turbulence in the boiler die down. This allows the temperature sensor to start gathering stable readings before the temperature management routines kick in. One minute works fine in most cases, but the larger the boiler, the longer the rest period will need to be. Yet another setting that you will need to tinker with to find your magic number.

<br><br><br>

## Third WebUI Data Card (third operation mode)

The third WebUI data card has a completely different collection of settings in the third operation mode. The **Brewing/Fermentation** mode turns the Boilermaker into a PID controller. If you are unfamiliar with the P, I, and D parameters of a PID controller, then I would recommend looking up tutorial videos on YouTube that explain how PID controllers work. This is quite a complex topic and far beyond the scope of this document. Let's just say that they are extremely precise and this procedure is much slower.

The PID controller code used in the Boilermaker is provided by an open source library called [QuickPID](https://github.com/Dlloydev/QuickPID) which has been developed and refined since January 2021. This was implemented in Boilermaker v1.0.2 in order to add a strict PID controller mode by request from numerous people wanting the Boilermaker to support beer brewing and fermentation temperature management.

_**PRO TIP:** PID controllers with boilers work best if you start them when the contents are already close to the target temperature._

**Target Temp:** The target temperature in this mode works exactly the same way as it does in **Temperature Cruise** mode.

**Proportional Gain:** This is the "P" in PID, the default setting is 1.0 in a new Boilermaker.

**Integral Gain:** This is the "I" in PID, the default setting is 0.005 in a new Boilermaker.

**Derivative Gain:** This is the "D" in PID, the default setting is 1.0 in a new Boilermaker.

**Sample Time:** This tunes the PID controller's number of calculations/updates per minute, the default setting is 10 seconds in a new Boilermaker. Higher powered heating elements or multiple heating elements would warrant a lower number. Slower heating elements or larger boiler volumes would warrant a higher number. The default is best suited for things like a 9 gallon DigiBoil or a 7 gallon Still Spirits T-500 boiler that run between 1500 and 1800 watts on a 120 volt supply.

**PWM Duty Time:** This tunes the low speed PWM that the Boilermaker uses to drive a solid state relay. This also works the same way as the **Sample Time** setting in the sense that the more efficient the heating element(s), the lower the number should be. But less efficient elements or larger boiler volumes will warrant a higher value. The default setting is 2.5 seconds in a new Boilermaker and should be adjusted to suit your boiler. Refer to the [Usage Tips](https://github.com/larry-athey/boilermaker/blob/main/Instructions/Usage-Tips.md) guide for more information.

## Fourth WebUI Data Card

The fourth WebUI data card is used to configure the countdown timer. In **Constant Power** mode, this timer begins as soon as you start your run. In all other modes, it only begins after the target temperature has been reached. This is primarily intended for brewing since a lot of times you need to hold a mash/wort at a specific temperature for a specific amount of time.

**Timer Enabled:** This is the on/off switch for the countdown timer function.

**Run Time:** This is the total number of minutes to run the timer from 1 to 1440 minutes (24 hours).

## Fifth WebUI Data Card

The last WebUI data card is only populated in **Temperature Cruise**, **Brewing/Fermentation**, and **Cruise Then Brew** modes. These settings allow you to do progressive temperature runs like the [Airhead](https://github.com/larry-athey/airhead) provides in Mode 3 with the only difference being that the Boilermaker doesn't shut down at the end of the progression. This progressively increases the target temperature every 15 minutes and resets back to the original target temperature when you stop the run.

In **Constant Power** mode, you naturally have a progressive temperature ramp which will continue to rise. This feature allows you to create that ramp with an actual end point that no longer continues to rise, but you can't precisely target that end point. In **Temperature Cruise** and **Brewing/Fermentation** modes with progressive temperature enabled, you actually can target the end point and the temperature rise time.

As you likely already figured out, you can combine this feature with the countdown timer in order to shut down the Boilermaker at the end of the progression.

**Progressive Run:** This is the on/off switch for the progressive temperature function.

**Progress Range:** This setting determines how much temperature increase that you want to add after the target temperature. You can add 1 to 50 degrees celcius to the target temperature. Keep in mind that every degree in celcius equals 1.8 degrees fahrenheit.

**Progress Time:** This setting determines how many hours that you want to spread the temperature increase. This timer only starts after the boiler has reached the target temperature and can be any value from 1 to 24 hours. The **Run State** line will change from "Active" to "Progressive" once this timer begins and will then say "* Active" once the progression is complete.

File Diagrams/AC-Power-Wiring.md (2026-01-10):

# AC Power Wiring

<br>

Pictured above is the inside of a Boilermaker that I'm preparing for an order placed on my website. This is one where a customer ordered it with the 120 volt 12 gauge pigtails. This should help those who  purchased the hard-wired version for a permanent installation, or intend to use it with a 240 volt boiler.

If you're looking at this Boilermaker from the front, the power input is on the left side. The neutral line (N) from the Boilermaker power supply line is connected to the first row of terminal bus bar on the bottom of the case and the hot line (L) is connected to the left AC terminal of the solid state relay.

The main AC power input lines connect to the same places as the Boilermaker's power supply wires. The ground wire from the main AC input cable connects to the third row of the terminal bus bar.

The AC power output to the boiler is on the right side. The hot wire connects to the right terminal of the solid state relay. The neutral wire connects to the second row of the terminal bus bar. The ground wire connects to the fourth row of the terminal bus bar.

A person can just as easily switch things around and use the right side as the power input, it doesn't matter which side of the solid state relay is used as the input or output.

**PRO TIP:** If your temperature sensor stops reading when it comes into contact with your boiler, your hot and neutral lines to the Boilermaker power supply are reversed or you have a defective ground connection. Double check your outlet with a plug-in outlet analyzer to make sure there are no problems with your AC power wiring at the outlet.

_**NOTE:** In the case of a 240 volt setup, you would just use the extra hot line in the place of the neutral line of the 120 volt wiring. The 240 volt neutral wires would just connect where the ground wires connect in the 120 volt wiring. If you happen to be using a 4-conductor cable (12/4 SOOW), the bus bar has an extra pair of jumped terminals for your ground wires._

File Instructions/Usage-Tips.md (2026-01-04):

# Boilermaker Usage Tips

_**NOTE:** Heating any boiler from the bottom-up often results in non-uniform temperature distribution—it's rarely linear across all levels due to how heat transfers in liquids. No controller can overcome fundamental physics or poor setup. To get the best results, a basic understanding of thermodynamics and fluid dynamics will help you set realistic expectations. Even the best tools only work correctly when used with care._

Although the Boilermaker adds temperature control to your boiler using both the **Temperature Cruise** and **Brewing/Fermentation** operating modes, it still needs to be tuned to your boiler. This isn't anything complicated and is done by simply heating up water to find the magic numbers that work with your setup. Even though an Air Still and a Still Spirits T500 system both accomplish the same end result, their settings are quite different. Compare the two below targeted at 80C/176F.

By default, the low speed PWM is set to a 2.5 second duty time. You will need to adjust this to match your heating element(s). You can find this setting near the bottom of the page when the **Brewing/Fermentation** mode is selected. The more efficient your heating element(s), the lower the duty time should be. The range is adjustable from 1 to 5 seconds. As you can see in the examples below, the Air Still's 700 watt element is very inefficient and requires a longer PWM duty time.

The examples below use the **Temperature Cruise** mode. This is the same temperature control method that's used in my [Airhead](https://github.com/larry-athey/airhead) upgrade for Air Stills. It's basically controlled chaos, it provides a rapid high thermal velocity temperature rise with a very limited risk of scorching because the temperature rise is linear, not just an instant constant blast of high power until the target temperature is reached. This mode is intended for pot still distillations or to preheat a **Brewing/Fermentation** run.

Air Still: 1 gallon, 700 watt 120 volt element running at 120 volts.
- Operation Mode: Temperature Cruise
- Target Temperature: 80.0C/176.0F
- Startup Power: 50%
- Fallback Power: 33%
- Adjustment Rate: 1%
- Deviation Rate: 0.2C
- Change Wait: 30 seconds
- Rest Period: 60 seconds
- SSR PWM Duty: 2.5 seconds

Still Spirits T500: 6 gallons, 1500 watt 120 volt element running at 120 volts.
- Operation Mode: Temperature Cruise
- Target Temperature: 80.0C/176.0F
- Startup Power: 75%
- Fallback Power: 25%
- Adjustment Rate: 1%
- Deviation Rate: 0.5C
- Change Wait: 30 seconds
- Rest Period: 60 seconds
- SSR PWM Duty: 1 second

Once they both do the fallback and stabilize, the Air Still will hover between 10% and 13%, the Still Spirits T500 will hover between 18% and 20%. Yes, they will actually work downward when targeting a temperature below the liquid's boiling point. These numbers will slightly vary when you have ethanol in the boiler and depending on your altitude. The Air Still will do its fallback well before hitting 100% power, the Still Spirits T500 will work up to 100% and stay there for about an hour before doing its fallback.

If you have a well insulated boiler or a jacketed boiler, you shouldn't be surprised to see the Boilermaker hover at less than 10%. The power level will never drop below 1% because this constant amount of at least some heat rising up through the boiler helps prevent suspended solids from falling out of solution and scorching to the bottom or your heating element. This was the primary problem that I was intending to cure when I came up with the [Airhead](https://github.com/larry-athey/airhead) project.

If you find that your boiler tends to run hot after the fallback and the Boilermaker always bottoms out to 1% power, reduce the PWM duty time. If you find that the boiler just takes forever to stabilize the temperature after fallback, increase the PWM duty time. 

## Using Your Boilermaker For Brewing and Fermentation

Some people ferment on the grain and some also distill on the grain if they have a boiler with a motorized paddle. Your Boilermaker can actually maintain fermentation temperatures by using the **Brewing/Fermentation** operating mode. This turns the Boilermaker into an actual PID controller with very strict tuning, which means that this is much slower than the **Temperature Cruise** mode.

_**NOTE:** This document isn't meant to be a tutorial on PID controllers, I recommend that you follow YouTube tutorial videos that explain them._

Keep in mind that you have a lot of suspended solids in brewing and fermentation. A PID controller may quickly wind up to 100% power depending on the current and target temperatures. This will almost always result in scorching. It's recommended that you first warm up your mash/wort in **Temperature Cruise** mode at a 25% Startup Power, 1-2 minute Change Wait, and a 1% Fallback Power. You would then switch to **Brewing/Fermentation** mode after the fallback. This guarantees no scorching and no over-shoot.

_**Remember,** the liquid at the bottom of your boiler is hotter than the top any time that the heating element is running. You may want to under-shoot your target temperature and allow stratification to complete before you increase your target temperature. For example, if your goal is 82.2C/180F, set your target temperature to 80C/176F and wait for stratification to complete, then increase your target temperature._

The placement of your temperature sensor also makes a major difference, mid-height of the boiler vessel is the best location. Too close to the bottom and the system will think that it's up to temperature before anything above it is. Too close to the top and you will likely end up scorching stuff at the bottom. Circulation pumps or motorized mixing paddles are an absolute necessity when you have a lot of solids.

Unlike some units on the market, this PID controller does not train itself and store any profile data in flash RAM. Every new run causes it to train itself from scratch. If you were to train the PID controller on plain water and then try to use that saved profile with a beer wort, you would end up scorching the suspended solids to your heating element.

_**PRO-TIP:** The **Cruise Then Brew** operation mode performs the above mode shift procedure automatically when the target temperature is reached. You can also use the progressive temperature function to automatically raise the target temperature up to your goal over 1 hour._

## Controlling An Electric Smoker

Aside from controlling boilers, another great use for the Boilermaker is turning any absolutely cheap bottom of the line electric smoker into a WiFi enabled **reliable and accurate** electric smoker. My first digital smoker got taken out by a lightning strike and I replaced it with a cheap [Masterbuilt steam smoker](https://www.amazon.com/gp/product/B07VRJQXGL/) and a $25 PID controller. Let's just say that PID controllers have their place, but they're really not the best option for a smoker since the heating element spends more time off than on.

With a PID controller, the heating element barely stays on long enough to get your wood chips smoldering. Whereas with the Boilermaker in **Temperature Cruise** mode, the power level usually never drops below 1%, so there is always some amount of heat coming from the heating element. Even with the default 2.5 second PWM duty time, 50% power means the heating element runs for 1.25 seconds before resting for 1.25 seconds, which is actually plenty enough heat to cause the wood chips to start smoldering.

Since a smoker can reach much higher temperatures than a boiler, you will might want to use a Type-K thermocouple rather than a DS18B20 temperature sensor or you'll never know when it gets above 125/257F in the smoker. Generally, this wouldn't be a problem with a smoker since people usually slow cook things between 107C/225F and 121C/250F. However, even I have had the random fire flare up in the smoker because grease dripped onto the red hot heating element.

I do have plans for making a WiFi enabled ESP32 powered temperature probe and timer unit for the Boilermaker and my [CZ Pellet Stove Controller](https://github.com/larry-athey/climate-czar/tree/main/CZ_Pellet_Stove_Controller_v2) with multiple temperature probes. I just have a few other programming projects that I need to tie up first. But I think it would be handy to have the capability to connect up to 4 probes and a timer to control the things and have it able to do an emergency shutdown if a fire is detected in the smoker. I'll get to this eventually, I'm just not exactly sure when that will happen.

Masterbuilt Steam Smoker Settings: 1800 watt 120 volt element running at 120 volts.
- Operation Mode: Temperature Cruise
- Target Temperature: 107.2C/225.0F
- Startup Power: 90%
- Fallback Power: 80%
- Adjustment Rate: 1%
- Deviation Rate: 0.5C
- Change Wait: 45 seconds
- Rest Period: 60 seconds
- SSR PWM Duty: 2.5 seconds

## The SCR vs SSR Debate

There really is no sense in trying to prove one is better than the other because they both do the same thing, just at different speeds. SCRs run hotter because they are turning the power on and off 120 times per second in the USA _(100 times per second in most other countries)_. This heat is what eventually leads to the failure of an SCR, moreso than overloading one. An SSR will also fail from too much heat because it's really not any different than an SCR when you look at what's inside of one.

The main complaint I see about SSRs is that the cheap Chinese ones are misrepresented, claims that some SSR-40DA units are actually only 15 amps. Even if that's the case, the only way that it will fail is if its triac gets too hot because it'll burn itself open. If you attach it to a large enough heatsink and use a fan to remove heat from it, they'll handle 40 amps just fine. The problem comes from them being attached to one of those tiny heatsinks or none at all, and having no fan cooling. Don't abuse it by overheating it, and it won't burn up.

The only real advantage that I can see that an SCR has is if you need to control the speed of an AC motor or the dimming of incandescent lights. An SSR really isn't intended for that kind of switching speed. The low speed switching of an SSR is perfect for heating elements, on/off switching, and anything else that needs to blink/flash slower than an SCR controller is capable of.

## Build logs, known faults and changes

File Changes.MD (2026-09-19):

Changes since the version 1.02 release

---

- Lots of WiFi related performance improvements and lost connection recovery enhancements. Today's WiFi 6 and 7 routers have a bad habit of putting devices to sleep if the router feels that they are unattended. This has been causing problems with some Boilermakers in the middle of a run where the only option was to unplug it and plug it back in before the router would allow it to reconnect. This sleep feature has now been disabled and will no longer obey these commands from the router.

- Cleaner hand-off to the PID controller in **Cruise Then Brew** mode. The PID controller no longer needs to play catch up, the power level is retained and the PID algorithm is updated along the way as the **Temperature Cruise** mode is gently ramping up the boiler temperature.

- PID auto tuning. This was added because no matter how you explain PID to somebody, it's still a rat-maze of if-then-else logic and most people aren't programmers. This requires your boiler to be full of water and the Boilermaker will first raise it to 66C/150F before the tuning begins, which takes 10 to 20 minutes after that point. Your web UI and API will become 100% unresponsive during this procedure and you only have 15 seconds to cancel it if you accidentally start it. The only output during this procedure is via serial connection.

- Correction factor range increased to match that of the Airhead/μBoilermaker (-15C to +15C). This increased range caters to people with boilers where the temperature sensor can only be mounted externally rather than inside of a thermowell.

- Over the air firmware updating. This was added so people can update the firmware without the need to install the full development environment. The Boilermaker becomes its own WiFi access point that you connect to and then simply upload the latest **boilermaker-firmware.bin** file with your web browser. Refer to the **/firmware/** directory of this GitHub repository for more information.

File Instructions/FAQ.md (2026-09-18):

# Frequently Asked Questions

Q: Why does the PID controller behave differently depending on what's in my boiler?

A: Because physics affects any temperature controller, whether it's PID or anything else. You can dial in your PID controller to reliably hold water at one temperature, but the moment you add grains to it, you've created insulating layers between the heating element and temperature sensor. PID controllers aren't a magic box, there is no AI running them. Learn what the P/I/D parameters actually do, start with P and no I or D, then add the I and D values as needed in small increments. Keep good notes for what works with different things that you boil.

---

Q: Why does the PID auto tuning fail or produce wild settings on my 120 volt, 1500 watt, 10 gallon boiler?

A: It all has to do with heating element efficiency and boiler volume. A 10 gallon boiler with a 120 volt, 1500 watt heating element is an extremely inefficient configuration. The more liquid volume you have, the more heating/cooling lag there is. With a small 1500 watt heating element fighting with 10 gallons, the heat it produces will move so slowly through the water that the auto tuning procedure will only collect partially useful results by the time it terminates. You're better off starting at zero on all three gain settings and then manually tuning them up.

---

Q: Why didn't you make this a Bluetooth device with a companion mobile app?

A: Bluetooth has a limited range _(20 to 40 feet in open spaces)_ and I'm not interested in paying all of the Apple developer fees just to put an app in their app store and keep it there. Google's Play Store isn't anywhere near as bad, but it still requires the expense of a code signing certificate. TCP/IP allows a person to monitor and control the Boilermaker anywhere on the network and the Web API wouldn't work without TCP/IP. Everybody already has a web browser on their phone or computer, so there's your app.

---

Q: What is the maximum wattage that the Boilermaker can handle?

A: That all depends on the solid state relay and wire that you use. The pre-assembled units that I sell on my website are shipped with an SSR-100DA on a massive aluminum heat sink _(as shown on the home page of this GitHub repo)_ and use a 50mm fan to constantly pull air through the heat sink during an active run. Standard 12-3 wire fits through the strain reliefs with the sheath and is capable of handling up to 20 amps, 10 guage _(30 amp)_ wire could be used, but with the sheath pulled back. Watts is calculated as volts * amps.

---

Q: Are there any plans to add volt/amp meter functionality to the Boilermaker's user interface?

A: No, and honestly this should be a meter on the outlet or junction box that you are tapped into because that's what you should be monitoring. Think about it, if you have a downstream cable heating up, that will eat current that your meter needs to run accurately. You want your meter upstream from that so that it can reliably warn you of any downstream problems. Those meters are dirt cheap, just connect it to your AC feed lines to the outlet or junction box and put the inductive donut around your hot wire.

---

Q: What's the reason for having the option of a digital temperature sensor or thermocouple?

A: Thermocouples aren't stable at low temperatures and the Boilermaker would be constantly chasing its tail at boiler temperatures with only a thermocouple. The digital temperature sensor is a much better choice for a boiler. If I limited the Boilermaker to only use the digital temperature sensor, then it would only be usable up to 125C/257F. Adding the option of also using a thermocouple allows the Boilermaker to run an electric grill or oven up to 260C/500F.

---

Q: Are these temperature sensors waterproof? As in, safe to insert into the liquid that I'm boiling?

A: Definitely not! They're water-safe against splashes and such, but not inside of boiling water. I realize that some vendors advertise DS18B20 sensors as "waterproof" but that's only safe at room temperature or less. Boiling water will quickly soften the heat shrink tubing and the epoxy inside of the metal cap. Once water gets in there, that sensor is done for. You need to use a thermowell and be sure to fill it with thermal compound before inserting the sensor.

---

Q: Why would my Boilermaker randomly become unreachable over my WiFi until I restart it?

A: Router configuration changes needed. Your router is likely set to WPA3 and/or has band steering enabled so it's trying to shove the Boilermaker over to the 5 GHz WiFi which it does not support. Switch to WPA2 and disable band steering by using a separate SSIDs for the 2.4 GHz and 5 GHz WiFi networks. Lastly, if you still have issues, look in your router's QoS section and add a reservation for your Boilermaker there. That basically puts a "DO NOT TOUCH" label on it so the router won't screw with it anymore.

---

Q: Are ISP-provided WiFi routers acceptable for use with a Boilermaker?

A: Unless the ISP gives you full administrative access to the router, then I say absolutely not. ISP tech support is 90% useless in most cases because all they know is what their internal documentation tells them. They won't help you troubleshoot anything any further than what their employee knowledge base covers. This is because __anybody__ can get hired for their job with absolutely zero experience. Get a decent router with decent tech support and online resources.

---

Q: I'm on fiber internet and my ISP provides their own required proprietary router with no admin access, what's my option here?

A: Get an inexpensive WiFi access point _(not an additional router or WiFi extender)_ that plugs into one of the ethernet ports of your existing router. This will provide a separate WiFi network that's bridged into your existing network. Disable the 5 GHz network and set it to WPA2. After that, you should be golden. TP-Link's budget EAP or WA series access points are great options. Again, do not try to use a router for this unless you know how to switch it into bridge or access point mode!

---

Q: All this WiFi and networking stuff is over my head, do you have a guide for this?

A: Sorry, that's way beyond the scope of what I'm doing here, but there are thousands of videos on YouTube that teach these topics. Honestly, I haven't seen too many cases where a person's WiFi is so flakey that they need any major help. The problematic cases that I've seen are usually caused by crappy outdated ISP-provided routers or by somebody intentionally making things hard for themselves. If you have a decent modern router, things will generally just work by default using nothing more than a DHCP (dynamic IP) address.

---

Q: Can you add charting and voice alerts to the Boilermaker like you have in your [RPi Smart Still](https://github.com/larry-athey/rpi-smart-still) controller?

A: The ESP32 that runs the Boilermaker doesn't have enough code space for this. I would recommend using an open source solution such as [Grafana](https://github.com/grafana/grafana) for this and set your own alarm functions within it to notify you audibly when specific criteria are met. There are plenty of YouTube tutorials covering the setup and usage of Grafana.

---

Q: Why do you have to enter all temperature settings in celcius?

A: This leans into the previous question, but it also comes down to the fact that the temperature sensors output in celcius. I have very little code space remaining in the ESP32 and wasting it on a bunch of temperature translation code is pointless. It's not just the web UI that would end up with code bloat, but also the web API as well. Most people always use the same temperatures anyway, it's not that hard to simply remember that 180F is 82.2C, 90F is 32.2C, you get the idea. The fact is, the majority of the world uses celcius anyway.

---

Q: Why are the wires on the two temperature sensors so short?

A: The longer the wire, the more resistance, the more chances for interference to wiggle its way into the system. If you need more distance, I recommend that you get your hands on some decent 3-conductor shielded microphone cable _(balanced, XLR)_ and use the shield as the ground connection. The heavier the gauge, the better _(no smaller than 18 gauge)_.

---

Q: My solid state relay is working just fine, but the on/off status LED isn't lighting up, why not?

A: That's just one of those oddities with solid state relays and low trigger voltages. The ESP32 puts out 3.3 volts and the solid state relay accepts a 3 to 32 volt trigger. However, the LED in those doesn't always light up at low voltages or they light up really dim _(some do, some don't)_. If yours isn't lighting up and you absolutely want one, just wire any LED in series with a 220 ohm resistor and connect it to the trigger terminals of the SSR _(cathode side connects to the negative terminal)_.

---

Q: Can I put the temperature sensor at the top of my distillation column rather than in the boiler?

A: You can, but you'll likely only do that one time and put it right back in the boiler after that. There's too much lag with that much distance between the sensor and the heat source, there's already more than enough lag through water alone. Putting the sensor even further away would have the power level going up and down like a yo-yo in both temperature managed modes. By the time the Boilermaker finally figures out what it's supposed to be doing, your distillation run will be over and done poorly.

---

Q: Can this be used to control a pellet fed grill/smoker, such as a Traeger?

A: No, but I have [another project](https://github.com/larry-athey/climate-czar/tree/main/CZ_Pellet_Stove_Controller_v2) that would work for that. Although, the precision would leave much too be desired since you can't just "put out a fire" in one of those with an ESP32 to cool it down. Electric smokers are easier to control, just kill the power if it's too hot.

---

Q: Do you offer any custom builds for people who would rather have this as a built-in feature in their existing setups?

A: No, but this project is 100% open source, anybody else is more than welcome to spin and remix things however they want to. I don't have anything in my home that gives me any kind of advantage over anybody else. Anybody can do everything that I'm doing and very easily one-up me because I'm half blind. I do sell assembled and tested Boilermaker PCB modules on https://panhandleponics.com if you want to make things a little easier on yourself.

---

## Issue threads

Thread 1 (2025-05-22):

Problem compiling

Mark-Kiwi, 2025-05-22:
Hi Larry,
I am trying to compile and upload the code but it is failing on me on the line
  timer = timerBegin(0,80,true); // Timer at 1 MHz, count up

I'm using IDE ver 1.8.13

I keep a log of what I've done as far as adding libraries, tweaking code so I know what I've done to make things compile. Here's what I did

added the following for esp32 support in the ide properties
https://dl.espressif.com/dl/package_esp32_index.json

In board manager select ESP32-Dev

In Library manager,

Needs ESP32Ping.h
Download from https://github.com/marian-craciunescu/ESP32Ping and copy to library folder

Install OneWire library ver 2.3.8 by Jim Studt,....

install Libraries for Dallas Semiconductor DS18B20 temperature sensor library
DallasTemperature by Miles Burton,... ver 4.0.3

Install Adafruit MAX-6675 amplifier library for Type-K thermocouples
MAX6675 library by Adafruit Ver 1.1.2

install HttpClient ver2.2.0
(Had errors so had to change the filenames in that library to match the code)
Changed the lowercase filenames in the library to
HTTPClient.http
HTTPClient.cpp

Compile...faults in web_ui.http...
'HttpClient' was not declared in this scope; did you mean 'HTTPClient'?

in web_ui.h file, changed
//  HttpClient http;
   HTTPClient http;

compile....

thats when I get the failure on
 timer = timerBegin(0,80,true); // Timer at 1 MHz, count up

The log is as follows...
-------------------------------------------------------------------------

C:\Users\EDS60001242\Documents\Arduino\Boiler_Brains_ver2\Boiler_Brains_ver2.ino: In function 'void setup()':
Boiler_Brains_ver2:148:21: error: too many arguments to function 'hw_timer_t* timerBegin(uint32_t)'
  148 |   timer = timerBegin(0,80,true); // Timer at 1 MHz, count up
      |           ~~~~~~~~~~^~~~~~~~~~~
In file included from C:\Users\EDS60001242\AppData\Local\Arduino15\packages\esp32\hardware\esp32\3.2.0\cores\esp32/esp32-hal.h:98,
                 from C:\Users\EDS60001242\AppData\Local\Arduino15\packages\esp32\hardware\esp32\3.2.0\cores\esp32/Arduino.h:45,
                 from sketch\Boiler_Brains_ver2.ino.cpp:1:
C:\Users\EDS60001242\AppData\Local\Arduino15\packages\esp32\hardware\esp32\3.2.0\cores\esp32/esp32-hal-timer.h:35:13: note: declared here
   35 | hw_timer_t *timerBegin(uint32_t frequency);
      |             ^~~~~~~~~~
Boiler_Brains_ver2:149:23: error: too many arguments to function 'void timerAttachInterrupt(hw_timer_t*, void (*)())'
  149 |   timerAttachInterrupt(timer,&onTimer,true); // Attach the PWM toggle function
      |   ~~~~~~~~~~~~~~~~~~~~^~~~~~~~~~~~~~~~~~~~~
C:\Users\EDS60001242\AppData\Local\Arduino15\packages\esp32\hardware\esp32\3.2.0\cores\esp32/esp32-hal-timer.h:50:6: note: declared here
   50 | void timerAttachInterrupt(hw_timer_t *timer, void (*userFunc)(void));
      |      ^~~~~~~~~~~~~~~~~~~~
Boiler_Brains_ver2:150:3: error: 'timerAlarmWrite' was not declared in this scope; did you mean 'timerWrite'?
  150 |   timerAlarmWrite(timer,SSR_PWM * 100000,true); // Timer trigger set to 2.5 seconds by default
      |   ^~~~~~~~~~~~~~~
      |   timerWrite
C:\Users\EDS60001242\Documents\Arduino\Boiler_Brains_ver2\Boiler_Brains_ver2.ino: In function 'void RunState(byte)':
Boiler_Brains_ver2:343:5: error: 'timerAlarmEnable' was not declared in this scope; did you mean 'timerAlarm'?
  343 |     timerAlarmEnable(timer);
      |     ^~~~~~~~~~~~~~~~
      |     timerAlarm
Boiler_Brains_ver2:360:5: error: 'timerAlarmDisable' was not declared in this scope
  360 |     timerAlarmDisable(timer);
      |     ^~~~~~~~~~~~~~~~~
C:\Users\EDS60001242\Documents\Arduino\Boiler_Brains_ver2\Boiler_Brains_ver2.ino: In function 'void loop()':
Boiler_Brains_ver2:705:21: error: 'timerAlarmDisable' was not declared in this scope
  705 |                     timerAlarmDisable(timer);
      |                     ^~~~~~~~~~~~~~~~~
Boiler_Brains_ver2:715:19: error: 'timerAlarmEnable' was not declared in this scope; did you mean 'timerAlarm'?
  715 |                   timerAlarmEnable(timer);
      |                   ^~~~~~~~~~~~~~~~
      |                   timerAlarm
Multiple libraries were found for "WiFi.h"
 Used: C:\Users\EDS60001242\AppData\Local\Arduino15\packages\esp32\hardware\esp32\3.2.0\libraries\WiFi
 Not used: C:\Program Files (x86)\Arduino\libraries\WiFi
exit status 1
too many arguments to function 'hw_timer_t* timerBegin(uint32_t)'

 -------------------------------------------------------------------------

Any thoughts on what I'm doing wrong?

Cheers!

Mark

larry-athey, 2025-05-22:
Try downgrading your ESP32 board library to version 2.x (I use 2.14 for everything). It appears to me that all of those v3.x board libraries aren't backward compatible with legacy boards.

Mark-Kiwi, 2025-05-22:
Thanks Larry I’ll give that a go tonight and let you know how i get on…it
might help others to know if they too are having issues.

(I’ve had problems like this before where a library needed to be reverted
to an earlier version before the code would compile… it mucked me around
for hours before I found the guilty library and the right version to
use, hence I now document my setup as much as possible in case I come back
at a later date and want to use that code again.)

Cheers!
Mark

On Thu, 22 May 2025 at 5:14 PM, Larry Athey ***@***.***>
wrote:

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

larry-athey, 2025-05-22:
I guess I didn't include the same note at the top of the .ino that I did with the Airhead code. I really wish they'd fix the system so the dependencies worked correctly. They've managed to solve this problem in the Linux world ever since the advent of the first package manager.

Mark-Kiwi, 2025-05-22:
Hey Larry!
Success! That was the trick...reverting the ESP32 board library to version 2.14 solved it.

To prove it, I did a clean install of the IDE using the latest version for the ESP32 board. Then installed just the required libraries and tried to compile,...interestingly I didn't have the issue of the compiler complaining about the case sensitivity like I did on the computer I used today (code using "HTTPClient.h" and the library file named "HttpClient.h"), but it did stop on the line
      timer = timerBegin(0,80,true); // Timer at 1 MHz, count up

So I then jumped into the board manager, reverted the ESP32 board library to version 2.14, ran the compiler again and this time it compiled without issue.

Thanks for the help! ....on with the build!

Cheers mate!

Mark

larry-athey, 2025-05-22:
I haven't seen that feature with the boot button in an ESP32 for a long time, but I do remember it with the very first one that I bought.

I saw a tip that said to install a 10uf electrolytic capacitor between the enable pin and ground and that solved it.

No idea what brand the board was, but I haven't had to do that with anything that I've bought since then.

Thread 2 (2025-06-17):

Powel level doesn't indicate lower than 10%

Mark-Kiwi, 2025-06-17:
Hiya Larry!
I have built my boilermaker (love it by the way) and am currently doing some testing and found something that I'm not sure if it is a bug or you have coded it that way by design.

The boilermaker sets the power level appropriately for heating, (starts at 100%, switches to 50% once at temperature, reduces power level if temp is over the target temp by more than deviation rate etc etc) ....But what I have noticed is that when the temperature is above the target temperature (by more than the deviation) and it starts dropping the power level, the power level displayed only drops as low as 10%, even though the SSR gets fully shut off. I would have thought it should read 0% at this point, only returning to 10% (and then climbing) once it's appropriate to start heating again.

It's not a big issue, and probably will only occur if this i used as a fermenting heat controller (ie the natural fermentation temperature goes above the target temp and the boilermaker shuts off) but thought I'd mention it.

Now to carry on building the smart still... (I'm going the 'prototype' build rather than the pi-hat version) pretty much have all of the boards built, just have to mount them, wire everthing up and then get it to talk to the boilermaker.

Cheers and keep up the great work!

Mark

larry-athey, 2025-06-20:
That's definitely one way to achieve it. I was just going to address it in the web UI and display "PWM Idle" instead of 0% because I know for sure that somebody will ask how to set the power level below 10% if they see it at 0% for any reason.

larry-athey, 2025-06-20:
The LiveData function in web_ui.h has been updated

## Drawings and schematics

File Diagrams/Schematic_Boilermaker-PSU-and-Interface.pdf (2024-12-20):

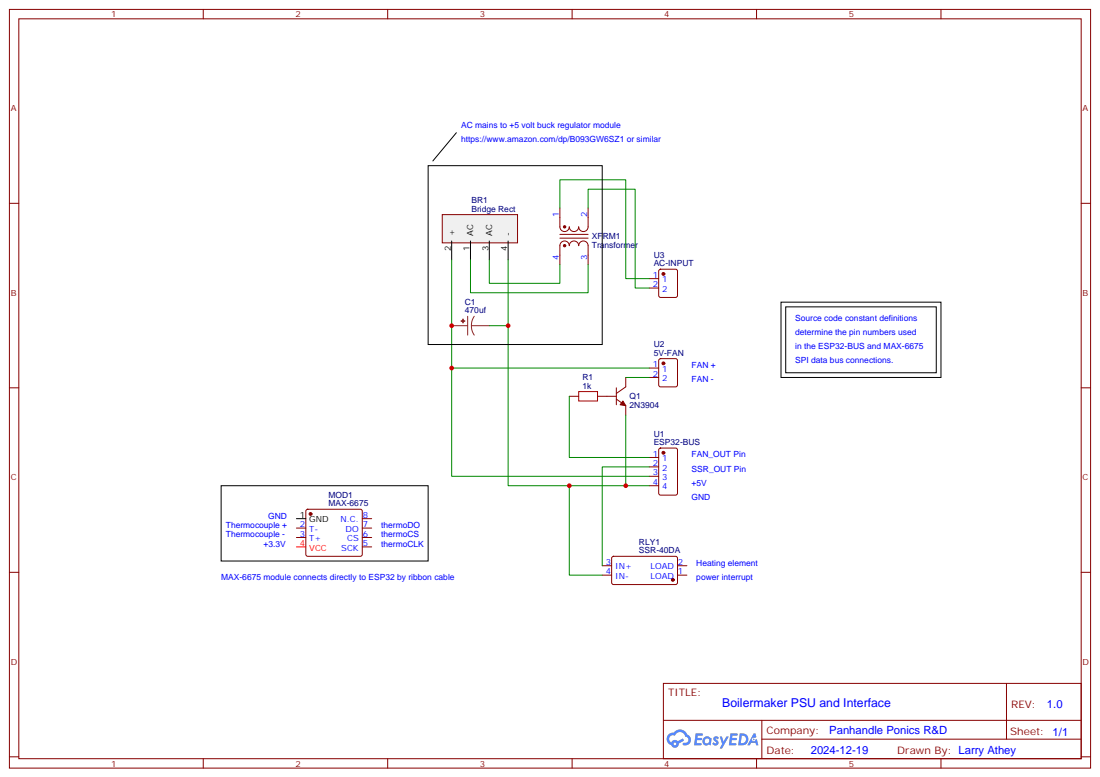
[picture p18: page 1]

AC mains to +5 volt buck regulator module
https://www.amazon.com/dp/B093GW6SZ1 or similar

Source code constant definitions
determine the pin numbers used
in the ESP32-BUS and MAX-6675

SPI data bus connections. FAN +

MAX-6675 module connects directly to ESP32 by ribbon cable

Drawn By: Larry Athey

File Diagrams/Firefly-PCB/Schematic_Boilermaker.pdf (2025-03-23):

# 29 18 30 19 31 GND 32 21 33 RX-3 34 TX-1 35 22 36 23 37 GND 38

# ESP 32DevkitC⁻v4

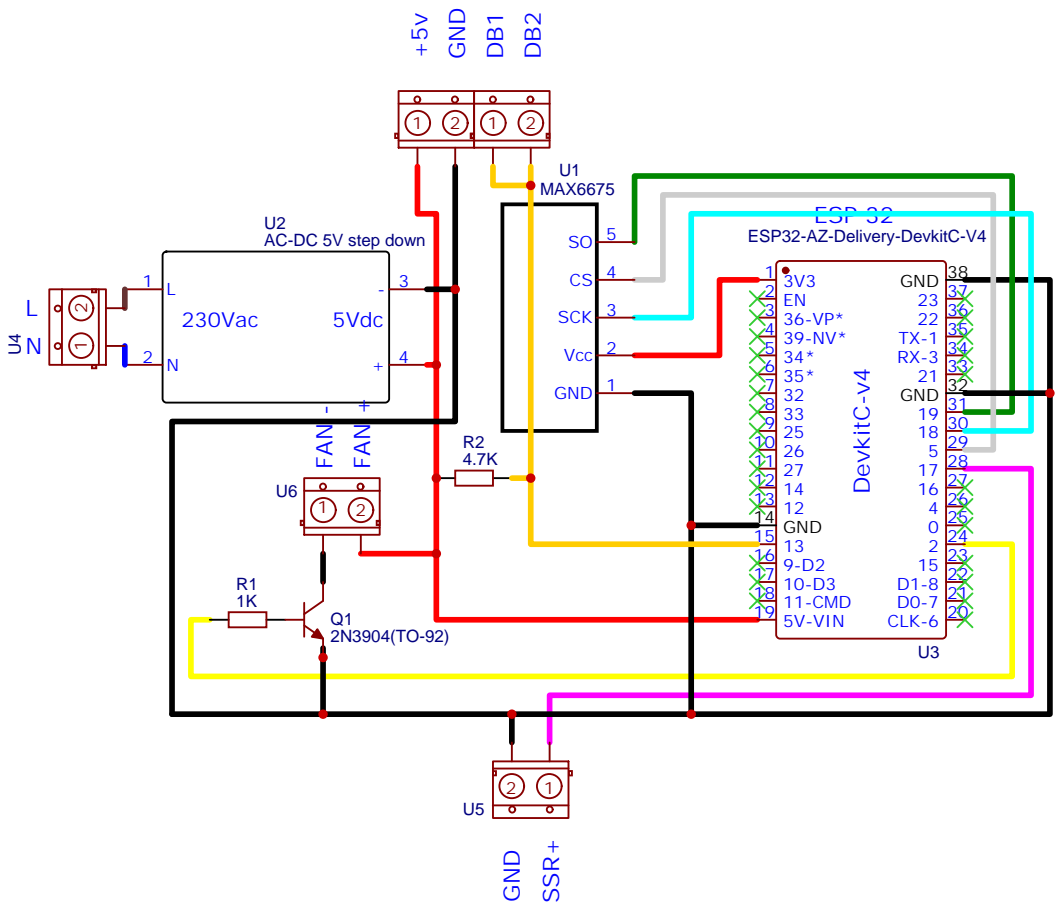
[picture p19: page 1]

AC-DC 5V step down

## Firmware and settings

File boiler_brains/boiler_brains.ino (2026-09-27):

//------------------------------------------------------------------------------------------------
// Boilermaker SCR/SSR Brain | (CopyLeft) 2024-Present | Larry Athey (https://panhandleponics.com)
//
// You must be using a v2.x ESP32 library to compile this code. It appears that v3.x libraries do
// not contain compatible headers for certain legacy libraries that I rely on. You should also use
// the following URL in your preferences under Additional Boards Manager URLs.
//
// https://raw.githubusercontent.com/espressif/arduino-esp32/gh-pages/package_esp32_index.json
//
// The project is based on the 38 pin ESP32 WROOM-32 using the v2.0.17 board library. The board
// selection I use is the "uPesy ESP32 Wroom DevKit" but you can use any other compatible board.
// This has been tested successfully with the WROOM-DA dual antenna board if you have the extra
// cash laying around and want to use the more expensive board.
//
// Derived from the boiler management routines in my Airhead upgrade for Air Stills (and clones).
// WiFi enabled with a built-in web interface that you can access from your phone's web browser to
// control the unit. Initial configuration to set up the WiFi connection is performed using a USB
// cable and serial terminal program such as PuTTY for Windows or CoolTerm for Mac OS.
//
// Each unit on the same WiFi network can either be a master or the default of stand-alone/slave.
// During the serial configuration, you just provide the IP addresses of all slave units and your
// unit instantly sees itself as the master. It will then run the slave units in sync with itself.
// This would be used in large boilers where you have multiple high wattage heating elements that
// need to run on separate circuits/phases. You may add up to 4 slave unit IP addresses.
//
// All configuration of the temperature and power management is performed using HTTP GET requests
// to the unit's web API. This is how a master unit controls slaves on the network. This can also
// be used to implement Boilermakers into other systems without the need to wire them in and add
// code for any other system's proprietary protocols. Use a script as a translator if necessary.
//
// This controller uses either a DS18B20 temperature sensor or a thermocouple which depends on a
// MAX-6675/MAX-31855 amplifier module. The DS18B20 is my normal go-to due to their low price and
// they ore perfectly fine for use in distillation projects since they have an upper temperature
// limit of 125C/257F. Set the default value of SensorType to 1 to use a thermocouple, or use the
// necessary Web API call with your web browser to change the temperature sensor type.
//
// NOTE: When using these controllers in a master/slave setup, all 4 slaves are ran in constant
//       power mode which follows the power level of the master controller. They are still able
//       to run independently in constant power or temperature managed modes, and will maintain
//       their own settings. Also, each slave can have its own 4 slaves as well that will follow
//       what this controller tells it to do. Think of it like an Amway pyramid scheme. LOL!!!
//------------------------------------------------------------------------------------------------
#include "WiFi.h"                // ESP32 high-level WiFi connectivity library
#include "esp_wifi.h"            // ESP32 low-level WiFi connectivity library
#include "HTTPClient.h"          // HTTP client library used for communicating with slave units
#include "ESP32Ping.h"           // ICMP (ping) library from https://github.com/marian-craciunescu/ESP32Ping
#include "ota_update.h"          // Over-The-Air firmware updating library
#include "Preferences.h"         // ESP32 Flash memory read/write library
#include "OneWire.h"             // OneWire Network communications library
#include "DallasTemperature.h"   // Dallas Semiconductor DS18B20 temperature sensor library
#include "max6675.h"             // Adafruit MAX-6675 amplifier library for Type-K thermocouples
#include "QuickPID.h"            // PID calculation library from https://github.com/Dlloydev/QuickPID
#include "sTune.h"               // QuickPID autotune library from https://github.com/Dlloydev/sTune
//------------------------------------------------------------------------------------------------
#define FAN_OUT 16               // Cooling fan on/off pin (to 1K resistor, to base of 2N3904 transistor) [The PCB has this on GPIO 2, so the onboard WiFi activity LED no longer works]
//#define SCR_OUT 17             // PWM output to an SCR board (comment out if using a zero-crossing SSR)
#define ONE_WIRE 13              // 1-Wire network pin for the DS18B20 temperature sensor
#define thermoMISO 19            // MAX-6675 SPI data bus
#define thermoCS 5               // "                   "
#define thermoCLK 18             // "                   "
//------------------------------------------------------------------------------------------------
#ifndef SCR_OUT
  #include "esp_timer.h"         // High resolution timer library for use with interrupt driven code
  #include "driver/gpio.h"       // ESP-IDF GPIO library
  #define SSR_OUT GPIO_NUM_17    // Same pin as used with an SCR board

  float SSR_PWM = 2.5;           // If using an SSR, how many seconds wide is the PWM duty?
  int dutyCyclePercentage = 0;   // Low frequency PWM duty cycle percentage
  hw_timer_t *timer = NULL;      // High resolution timer library
#endif
//------------------------------------------------------------------------------------------------
OneWire oneWire(ONE_WIRE);
DallasTemperature DT(&oneWire);
MAX6675 thermocouple(thermoCLK,thermoCS,thermoMISO);
Preferences preferences;
WiFiServer Server(80);
//------------------------------------------------------------------------------------------------
bool ActiveRun = false;          // True if there's an active heating run
bool UpToTemp = false;           // True if the run startup has reached operating temperature
bool PWMenabled = false;         // True if the low speed PWM is enabled
bool TimerEnabled = false;       // True if the countdown timer is enabled;
bool TimerStarted = false;       // True if the countdown timer has started;
bool FWupdate = false;           // True if the system should start up in OTA firmware update mode
bool UpdateMode = false;         // True if the Boilermaker is running in firmware update mode
long Countdown = 0;              // Seconds left on the countdown timer
long LoopCounter = 0;            // Timekeeper for the loop to eliminate the need to delay it
long StartTime = 0;              // Start time of the current heating run
long LastAdjustment = 0;         // Time of the last power adjustment
long FallBackTime = 0;           // Time that TargetTemp was reached
float TempC = 0;                 // Current temperature reading C
float TempF = 0;                 // Current temperature reading F
float CorrectionFactor = 0;      // How much to correct temp sensor C readings (positive or negative)
float TargetTemp = 80;           // Target temperature (C) if OpMode = 1 is selected
float Deviation = 1;             // How many degrees the temperature is allowed to deviate
int ChangeWait = 120;            // How many seconds to wait between power adjustments
int CountdownMinutes = 90;       // How many minutes to run the countdown timer
int RestPeriod = 60;             // Seconds to wait after fall back before temperature management
byte SensorType = 1;             // Selected temperature sensor type: 0=MAX6675, 1=DS18B20
byte SlavesPinging = 0;          // Shows how many configured slaves are actually online
byte AdjustRate = 1;             // How much power % change to make when temperature is out of range
byte FallBackPercent = 50;       // Power % to fall back to when TargetTemp has been reached
byte StartupPercent = 50;        // Power % to start at or target power in OpMode 0
byte TuningStartup = 0;          // Used as a delay timer for the PID auto tuning to make sure the UI is fully updated
byte PowerLevel = 0;             // Current power level 0-255
byte OpMode = 1;                 // Operation mode, 0 = Constant Power, 1 = Temperature Cruise, 2 = Brewing/Fermentation
byte wifiCheckCounter = 0;       // Used to check the WiFi connection once per minute
byte wifiMode = 0;               // DHCP (0) or manual configuration (1)
String wifiSSID = "none";        // WiFi network SSID
String wifiPassword;             // WiFi network password
String wifiIP;                   // WiFi network IPV4 address
String wifiMask;                 // WiFi network subnet mask
String wifiGateway;              // WiFi network default gateway address
String wifiDNS;                  // WiFi network DNS resolver address
String slaveIP1 = "";            // Slave unit 1 IPV4 address
String slaveIP2 = "";            // Slave unit 2 IPV4 address
String slaveIP3 = "";            // Slave unit 3 IPV4 address
String slaveIP4 = "";            // Slave unit 4 IPV4 address
String DeviceName;               // Network host name and device name to be displayed in the web UI
String Uptime = "00:00:00";      // Current system uptime
String Runtime = "00:00:00";     // Current heating runtime
String TimeLeft = "00:00:00";    // Countdown time remaining
String TuningData = "n/a";       // PID auto tuning result data
String Version = "1.0.3d";       // Current release version of the project
//------------------------------------------------------------------------------------------------
// v1.0.2 add-on to provide Airhead style progressive temperature control
bool ProgressEnabled = false;    // True if progressive temperature is enabled
bool ProgressStarted = false;    // True if the original target temperature has been reached
float SavedTarget = 0;           // Used to restore the TargetTemp setting at the end of a progressive temp run
float ProgressFactor = 0.0;      // How much to increase the target temperature every 15 minutes
byte ProgressHours = 4;          // How many hours to spread ProgressRange over
byte ProgressRange = 10;         // How many degrees C to increase TargetTemp over the course of ProgressHours
int pTimer = 0;                  // 15 minute (900 second) timer placeholder
//------------------------------------------------------------------------------------------------
// v1.0.2 add-on to provide PID control in OpMode 2 (Brewing/Fermentation)
float pidOutput = 0.0;           // PID Computed PWM percentage (0-100)
float Kp = 0.1;                  // PID Proportional gain (0.1 to 15.0)
float Ki = 0.029;                // PID Integral gain (0.001 to 0.5)
float Kd = 0.1;                  // PID Derivative gain (0.0 to 2.0)
float sampleTime = 10.0;         // PID Sample time (5 to 30 seconds)
QuickPID myPID(&TempC,&pidOutput,&TargetTemp,Kp,Ki,Kd,
               QuickPID::pMode::pOnMeas,
               QuickPID::dMode::dOnMeas,
               QuickPID::iAwMode::iAwCondition,
               QuickPID::Action::direct);
// v1.0.3 add-on to provide PID auto tuning
sTune tuner(&TempC,&pidOutput,
            sTune::ZN_PID,
            sTune::directIP,
            sTune::printSUMMARY);
//------------------------------------------------------------------------------------------------
#include "slave_sync.h"          // Library for configuring and synchronizing slave units
#include "serial_config.h"       // Library for configuring WiFi connection and slave unit IP addresses
#include "web_ui.h"              // Library for the web user interface and HTTP API implementation
//-----------------------------------------------------------------------------------------------
#ifndef SCR_OUT
void IRAM_ATTR onTimer() { // Custom low frequency PWM designed specifically for SSR usage
  static uint32_t cycleCounter = 0;
  cycleCounter ++;
    
  if (cycleCounter == 10) { // Reset counter every 10 interrupts
    cycleCounter = 0;
  }

  if (cycleCounter < (dutyCyclePercentage / 10.0)) { // Turn on if within duty cycle
    gpio_set_level(SSR_OUT,1);
  } else {
    gpio_set_level(SSR_OUT,0);
  }
}
#endif
//------------------------------------------------------------------------------------------------
void setup() {
  // Enable serial communications for WiFi setup and slave IP address management
  Serial.begin(9600);
  Serial.setDebugOutput(false);
  delay(1000);
  PurgeBuffer();
  if (Serial) Serial.println("");

  // Get the last user settings from flash memory
  GetMemory();
  if (wifiSSID == "none") {
    SetMemory();
  } else {
    if ((wifiSSID != "none") && (wifiPassword != "") && (! FWupdate)) ConnectWiFi();
  }

  #ifndef SCR_OUT
  // Custom interrupt driven low speed (.1 Hz to 1 Hz) PWM for driving a solid state relay
  gpio_set_direction(SSR_OUT,GPIO_MODE_OUTPUT);
  gpio_set_level(SSR_OUT,0);
  timer = timerBegin(0,80,true); // Timer at 1 MHz, count up
  timerAttachInterrupt(timer,&onTimer,true); // Attach the PWM toggle function
  timerAlarmWrite(timer,SSR_PWM * 100000,true); // Timer trigger set to 2.5 seconds by default
  #else
  // Assign the SCR controller output pin to a PWM channel
  // For heating elements, 1 KHz to 3 KHz is used, adjust as necessary
  ledcSetup(1,2000,8);
  ledcAttachPin(SCR_OUT,1);
  ledcWrite(1,0);
  #endif
 
  myPID.SetOutputLimits(0,100);
  myPID.SetSampleTimeUs(sampleTime * 1000000); // 10 second sample time (adjustable from 5 to 30 seconds)
  myPID.SetMode(myPID.Control::automatic);

  DT.begin();
  pinMode(FAN_OUT,OUTPUT); 
  digitalWrite(FAN_OUT,LOW);
  LoopCounter = millis();
  LastAdjustment = LoopCounter;

  // FWupdate is only true if the API call was made to activate the OTA firmware updater
  if (FWupdate) {
    FWupdate = false;
    SetMemory();
    Server.end();
    UpdateMode = true;

    Serial.println("Starting Airhead Firmware Updater (AP mode)...");

    // Start WiFi Access Point
    WiFi.mode(WIFI_AP);
    uint8_t protocol = WIFI_PROTOCOL_11B | WIFI_PROTOCOL_11G | WIFI_PROTOCOL_11N;
    esp_wifi_set_protocol(WIFI_IF_AP,protocol);
    esp_wifi_set_bandwidth(WIFI_IF_AP,WIFI_BW_HT20);
    esp_wifi_set_max_tx_power(84);
    WiFi.softAP(ap_ssid,ap_password,6);
    IPAddress myIP = WiFi.softAPIP();
    Serial.print("AP IP address: ");
    Serial.println(myIP);

    // Start Bonjour/ZeroConf
    if (MDNS.begin("esp32")) {
      Serial.println("mDNS started - http://esp32.local");
    }

    // Set the server home page, sent upon browser connection
    server.on("/",HTTP_GET,[]() {
      server.send(200,"text/html",serverIndex);
    });

    // Set the OTA firmware update handler
    server.on("/update",HTTP_POST,[]() {
      server.sendHeader("Connection","close");
      server.send(200,"text/plain",(Update.hasError()) ? "FAIL" : "OK");
      ESP.restart();
    },[]() {
      HTTPUpload& upload = server.upload();
      if (upload.status == UPLOAD_FILE_START) {
        Serial.printf("Update: %s\n",upload.filename.c_str());
        if (!Update.begin(UPDATE_SIZE_UNKNOWN)) {
          Update.printError(Serial);
        }
      } else if (upload.status == UPLOAD_FILE_WRITE) {
        if (Update.write(upload.buf,upload.currentSize) != upload.currentSize) {
          Update.printError(Serial);
        }
      } else if (upload.status == UPLOAD_FILE_END) {
        if (Update.end(true)) {
          Serial.printf("Update Success: %u bytes\n",upload.totalSize);
        } else {
          Update.printError(Serial);
        }
      }
    });

    server.begin();
    Serial.println("HTTP server ready. Connect to the AP and go to 192.168.4.1");

  } else {
    if (Serial) {
      ShowConfig();
      ConfigMenu();
    }
  }
}
//------------------------------------------------------------------------------------------------
void ConnectWiFi() { // Connect to WiFi network, must be WPA2-PSK, not WPA3
  byte x = 0;
  if (Server) Server.end();
  WiFi.mode(WIFI_STA);
  WiFi.setSleep(false);
  WiFi.setAutoReconnect(true);
  WiFi.persistent(true);

  uint8_t protocol = WIFI_PROTOCOL_11B | WIFI_PROTOCOL_11G | WIFI_PROTOCOL_11N;
  esp_wifi_set_protocol(WIFI_IF_STA,protocol);
  esp_wifi_set_bandwidth(WIFI_IF_STA,WIFI_BW_HT20);
  esp_wifi_set_max_tx_power(84);
  if (wifiMode == 1) {
    bool Passed = true;
    int segCount = 0;
    int ipSegments[4];
    int maskSegments[4];
    int gwSegments[4];
    int dnsSegments[4];
    segCount = sscanf(wifiIP.c_str(),"%d.%d.%d.%d",&ipSegments[0],&ipSegments[1],&ipSegments[2],&ipSegments[3]);
    if (segCount != 4) {
      if (Serial) Serial.println("\nCannot parse static IP address!");
      Passed = false;
    }
    segCount = sscanf(wifiMask.c_str(),"%d.%d.%d.%d",&maskSegments[0],&maskSegments[1],&maskSegments[2],&maskSegments[3]);
    if (segCount != 4) {
      if (Serial) Serial.println("\nCannot parse subnet mask!");
      Passed = false;
    }
    segCount = sscanf(wifiGateway.c_str(),"%d.%d.%d.%d",&gwSegments[0],&gwSegments[1],&gwSegments[2],&gwSegments[3]);
    if (segCount != 4) {
      if (Serial) Serial.println("\nCannot parse gateway address!");
      Passed = false;
    }
    segCount = sscanf(wifiDNS.c_str(),"%d.%d.%d.%d",&dnsSegments[0],&dnsSegments[1],&dnsSegments[2],&dnsSegments[3]);
    if (segCount != 4) {
      if (Serial) Serial.println("\nCannot parse DNS resolver address!");
      Passed = false;
    }
    if (Passed) {
      IPAddress staticIP(ipSegments[0],ipSegments[1],ipSegments[2],ipSegments[3]);
      IPAddress subnet(maskSegments[0],maskSegments[1],maskSegments[2],maskSegments[3]);
      IPAddress gateway(gwSegments[0],gwSegments[1],gwSegments[2],gwSegments[3]);
      IPAddress dns(dnsSegments[0],dnsSegments[1],dnsSegments[2],dnsSegments[3]);
      if (! WiFi.config(staticIP,gateway,subnet,dns,dns)) {
        if (Serial) Serial.println("\nWiFi static IP configuration failed!");
        delay(2000);
      }
    } else {
      delay(2000);
    }
  }
  WiFi.setHostname(DeviceName.c_str());
  WiFi.begin(wifiSSID,wifiPassword);
  if (Serial) Serial.print("\nConnecting to WiFi ..");
  while (WiFi.status() != WL_CONNECTED) {
    if (Serial) Serial.print('.');
    delay(1000);
    x ++;
    if (x == 15) break;
  }
  if (WiFi.status() == WL_CONNECTED) {
    Server.begin();
    wifiIP = WiFi.localIP().toString();
    wifiMask = WiFi.subnetMask().toString();
    wifiGateway = WiFi.gatewayIP().toString();
    wifiDNS = WiFi.dnsIP(0).toString();
    SlavesPinging = PingAllSlaves();
  } else {
    wifiIP = "";
    wifiMask = "";
    wifiGateway = "";
    wifiDNS = "";
    if (Serial) Serial.println("\nConnection Failed!");
    delay(2000);
  }
}
//------------------------------------------------------------------------------------------------
void GetMemory() { // Get the configuration settings from flash memory on startup
  preferences.begin("prefs",true);
  wifiMode         = preferences.getUInt("wifi_mode",0);
  wifiSSID         = preferences.getString("wifi_ssid","none");
  wifiPassword     = preferences.getString("wifi_password","");
  wifiIP           = preferences.getString("wifi_ip","");
  wifiMask         = preferences.getString("wifi_mask","");
  wifiGateway      = preferences.getString("wifi_gateway","");
  wifiDNS          = preferences.getString("wifi_dns","");
  DeviceName       = preferences.getString("device_name","Boilermaker-" + WiFi.macAddress());
  slaveIP1         = preferences.getString("slave1","");
  slaveIP2         = preferences.getString("slave2","");
  slaveIP3         = preferences.getString("slave3","");
  slaveIP4         = preferences.getString("slave4","");
  CorrectionFactor = preferences.getFloat("correction",0.0);
  OpMode           = preferences.getUInt("op_mode",1);
  TargetTemp       = preferences.getFloat("target_temp",80.0);
  StartupPercent   = preferences.getUInt("startup_percent",50);
  FallBackPercent  = preferences.getUInt("fb_percent",50);
  AdjustRate       = preferences.getUInt("adjust_rate",1);
  Deviation        = preferences.getFloat("deviation",1.0);
  ChangeWait       = preferences.getUInt("change_wait",120);
  RestPeriod       = preferences.getUInt("rest_period",60);
  SensorType       = preferences.getUInt("sensor_type",1);
  ProgressEnabled  = preferences.getBool("prog_enabled",false);
  ProgressHours    = preferences.getUInt("progress_hours",4);
  ProgressRange    = preferences.getUInt("progress_range",10);
  Kp               = preferences.getFloat("pid_kp",1.0);
  Ki               = preferences.getFloat("pid_ki",0.005);
  Kd               = preferences.getFloat("pid_kd",1.0);
  sampleTime       = preferences.getFloat("pid_sampletime",10.0);
  TimerEnabled     = preferences.getBool("timer_enabled",false);
  CountdownMinutes = preferences.getUInt("timer_minutes",90);
  FWupdate         = preferences.getBool("fw_update",false);
  #ifndef SCR_OUT
  SSR_PWM          = preferences.getFloat("ssr_pwm",2.5);
  #endif
  preferences.end();
}
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
void loop() {

}
*/
//------------------------------------------------------------------------------------------------

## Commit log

2025-03-23 PCB by Mathias added
2025-03-23 PCB file name updates
2025-03-31 Web UI and model updates
    [BM-ESP32-Cover.stl]
2025-04-05 Upload new models for use with the PCB
    [BM-Case-Bottom.stl, BM-Case-Top.stl, BM-Fan-Cover.stl]
2025-04-06 PCB support model updates
    [BM-Case-Bottom.stl]
2025-04-06 ESP32 code update to add temperature sensor type selection via API
    [BM-Case-Bottom.stl]
2025-04-07 Add photos of the new case for PCB based builds
2025-04-27 Minor adjustments to internal device placement
    [BM-Case-Bottom.stl]
2025-12-19 Initial implementation of PID OpMode
